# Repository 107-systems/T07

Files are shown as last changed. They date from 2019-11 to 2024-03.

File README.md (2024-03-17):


T07
===

T07 is a wheeled mobile outdoor robotics platform.

### Repositories
* [t07_robot](https://github.com/107-systems/t07_robot): ROS control code for T07 robot.
* [t07_docker](https://github.com/107-systems/t07_docker): Dockerfile and scripts to run T07 control software on [Pika Spark](https://pika-spark.io/).
* [t07_teleop](https://github.com/107-systems/t07_teleop): Keyboard based teleoperation for the T07 mobile outdoor robot.

### 3D-Renderings

<p align="center">
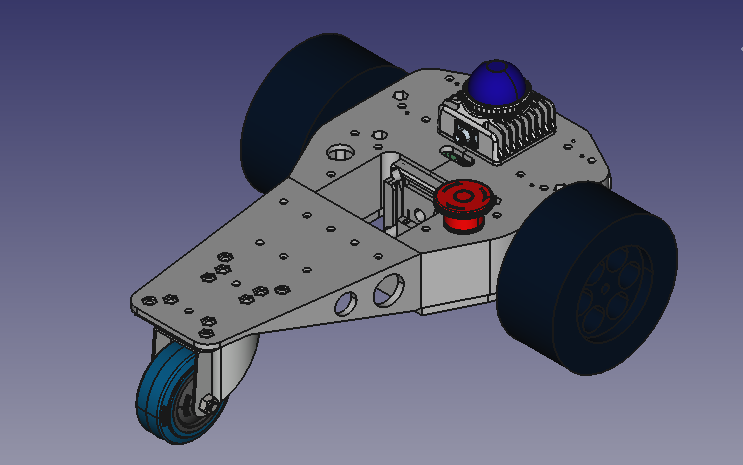
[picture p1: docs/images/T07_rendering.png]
   
</p>

<p align="center">
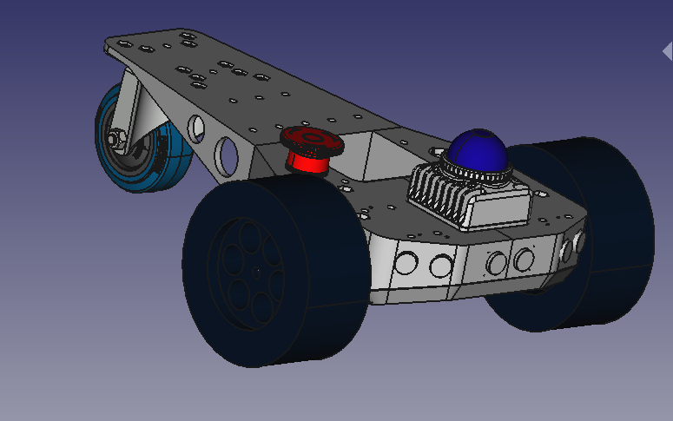
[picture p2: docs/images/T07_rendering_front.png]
   
</p>

<p align="center">
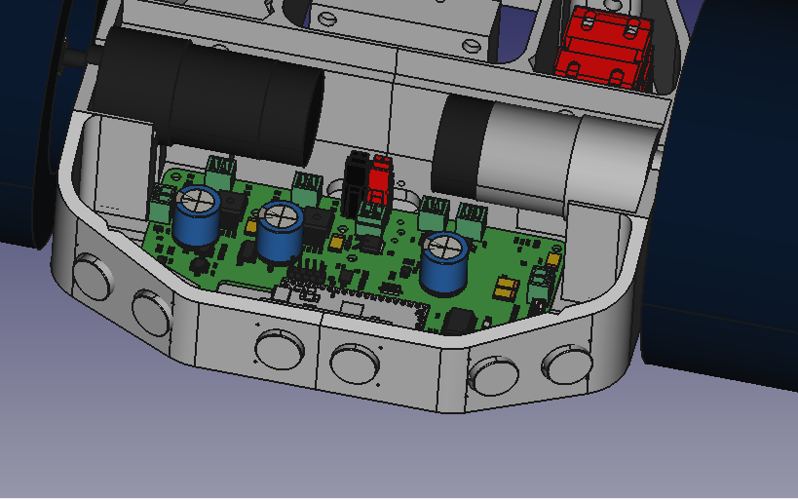
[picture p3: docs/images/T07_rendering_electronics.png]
   
</p>

<p align="center">
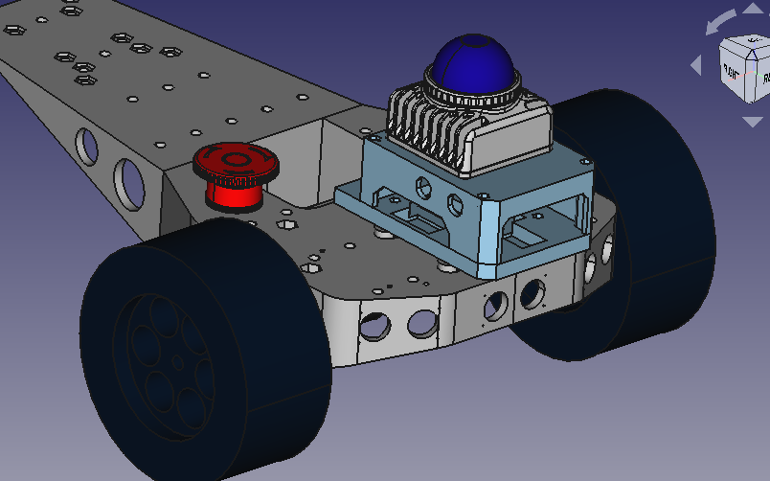
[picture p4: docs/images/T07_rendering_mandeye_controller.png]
   
</p>

## Introduction

The T07 is an outdoor robotics platform intended for participation in contests like Robotem Rovne, Roboorienteering or Robotour but also for general robotic experiments.

There is also a mounting option for the [mandeye-controller](https://github.com/JanuszBedkowski/mandeye_controller).

## Special configurations

### T07 4WD

<p align="center">
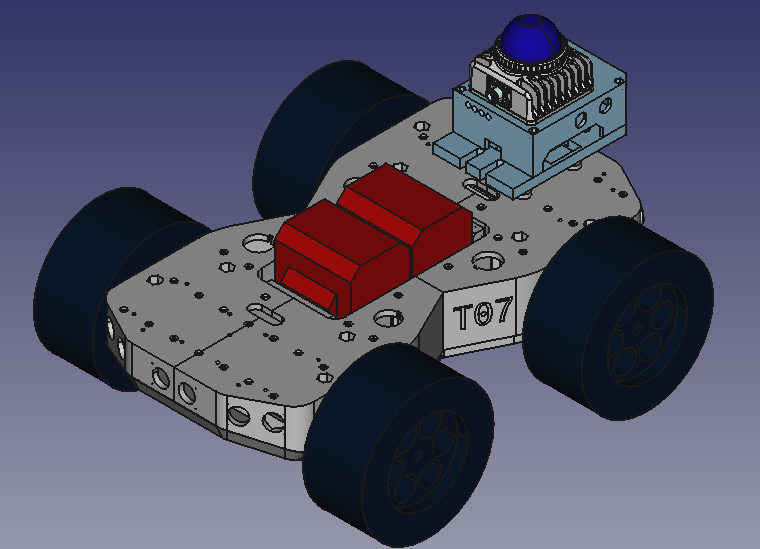
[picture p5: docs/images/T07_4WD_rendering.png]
   
</p>

### T07 low profile

<p align="center">
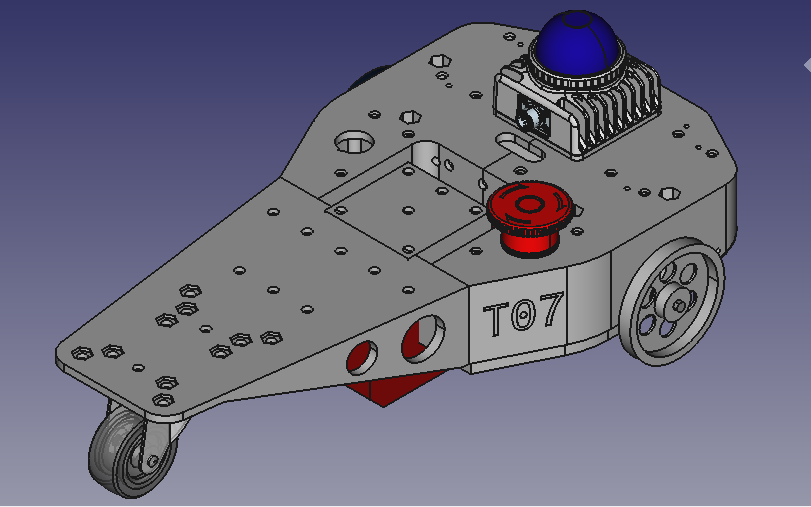
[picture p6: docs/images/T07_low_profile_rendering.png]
   
</p>

<p align="center">
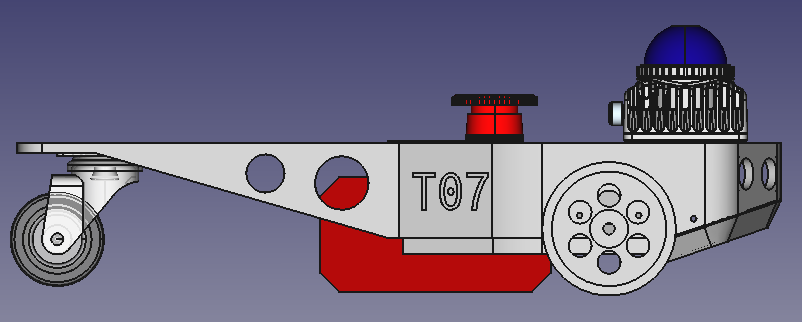
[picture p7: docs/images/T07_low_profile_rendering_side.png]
   
</p>

## Dimensions

The chassis is 40 cm long and 20 cm wide.

The whole robot with ultrasonic sensors is depending on the wheels about 45 cm long and 35 cm wide. The weight is about 1.5 kg.

### Motor shaft and wheel dimension

There are 2 positions to mount the motor shaft.

| Motor shaft | Shaft to roller wheel base | Roller wheel height | Recommended wheel diameter |
|---|---|---|---|
| Upper position | 20 mm | 100 mm (70 mm diameter) | 160 mm |
| Lower position | 34 mm | 100 mm (70 mm diameter) | 132 mm |
| Lower position | 34 mm | 70 mm (50 mm diameter)  | 72 mm |

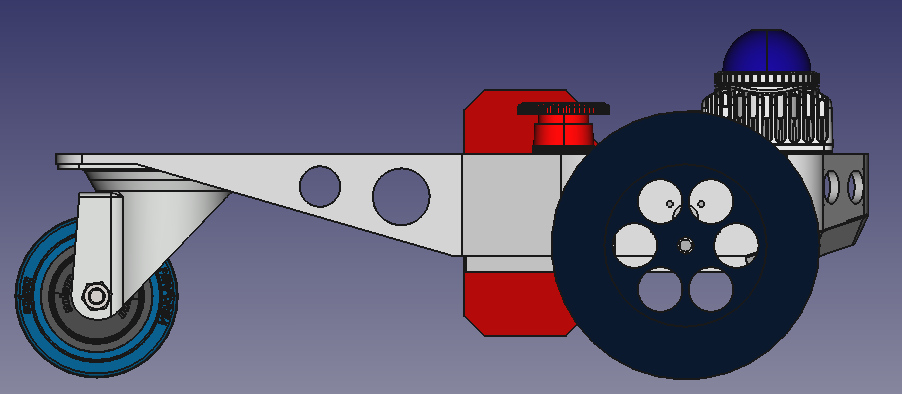
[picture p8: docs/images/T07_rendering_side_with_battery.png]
T07 rendering side view with battery


## Battery

This robot is designed to work with the [Einhell Power X-Change system](https://www.einhell.de/en/battery-system/).

## Assembly

Use flat M6 screw nuts (DIN 439, 3.2 mm high) for the assembly.

## Additional required hardware

### Motors

A motor with a gear ratio of about 1:100 should be ok.

#### Standard

  * https://www.reichelt.de/getriebemotor-39-6-mm-75-1-12-v-dc-gm39-6-75-12v-p159644.html
  * https://www.conrad.de/de/p/getriebemotor-12-v-modelcraft-rb350100-0a101r-1-100-227560.html

#### With encoder

  * https://de.sainsmart.com/products/29-1-metal-gearmotor-365rpm-37dx52l-mm-with-64-cpr-encoder-12v
  * https://eu.robotshop.com/de/products/12v-58rpm-60-1-gear-motor-encoder
  * https://eu.robotshop.com/de/products/12v-26rpm-1201-gear-motor-w-encoder

### Wheels

please pay attention to get the right wheel adapter

#### 132 mm

  * https://www.conrad.de/de/p/reely-1-10-monstertruck-komplettraeder-schwarz-2-st-2249111.html

#### 160 mm

  * https://www.conrad.de/de/p/reely-1-6-buggy-komplettraeder-block-spike-8-speichen-schwarz-glaenzend-2-st-2159621.html

#### 70 mm

  * https://eu.robotshop.com/products/70mm-aluminium-wheel-6mm-bore

### Wheel Adapter

  * https://www.pololu.com/product/2687
  * https://eckstein-shop.de/Pololu-12mm-Hex-Wheel-Adapter-for-6mm-Shaft-Extended-2-Pack

### Roller wheel

#### 100 mm height (70 mm diameter)

  * https://www.pollin.de/p/laufrolle-441614
  * https://radundrolle.de/seiten/Lenkrollen/Vollgummi-Lenkrolle_080.htm

#### 70 mm height (50 mm diameter)

  * https://www.pollin.de/p/masterproof-lenkrolle-kugelgelagert-4054-pvc-oe-50-mm-490596

### On/off Switch

  * https://www.reichelt.de/wippenschalter-rund-ip65-1x-ein-aus-sw-sw-ws-r13-112-a-sw-p105455.html

### Emergency Switch

  * https://www.reichelt.de/not-aus-schalter-yw-40-mm-2-nc-id-yw1bv4e02r-p234555.html
  * https://www.conrad.de/de/p/idec-yw1b-v4e01r-not-aus-schalter-240-v-ac-6-a-1-oeffner-1-st-700792.html
  * https://www.conrad.de/de/p/deca-a20b-v4e11r-not-aus-schalter-mit-kontaktelement-240-v-ac-6-a-1-schliesser-1-oeffner-ip65-1-st-1233793.html

## Electronics and firmware

There are mounting holes for a Raspberry Pi or a [Pika Spark](https://docs.pika-spark.io/) on the controller standoff.

[CyphalRobotController07/CAN](https://github.com/generationmake/CyphalRobotController07-CAN) is the main controller board.

## License

This hardware is licensed under the Creative Commons licence CC-BY-SA 4.0

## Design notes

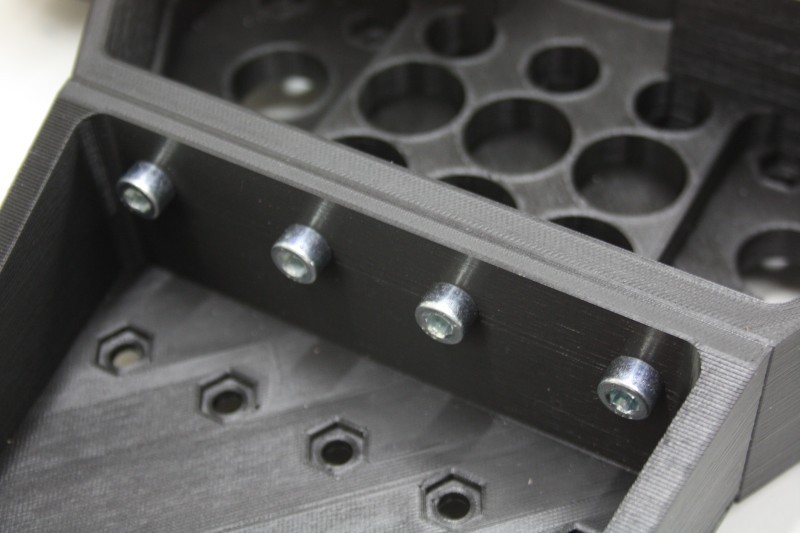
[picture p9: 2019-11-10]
docs/images/chassisconnection_2.jpg

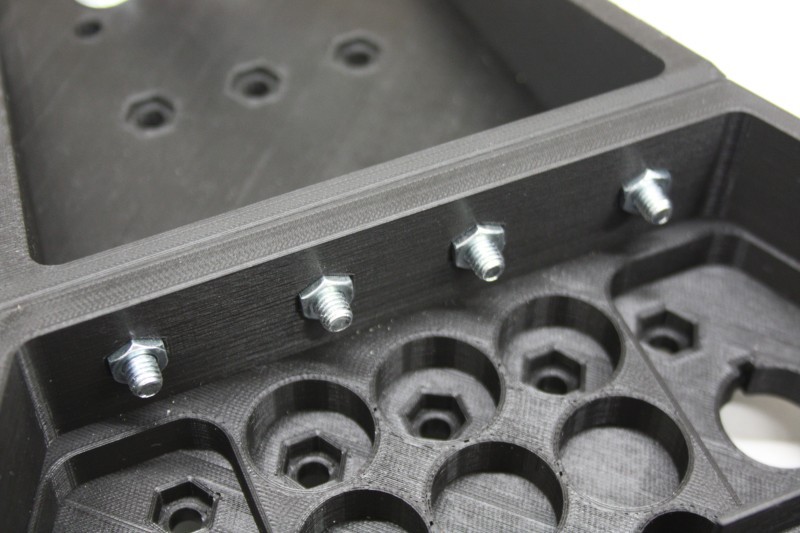
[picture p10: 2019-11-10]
docs/images/chassisconnection_1.jpg

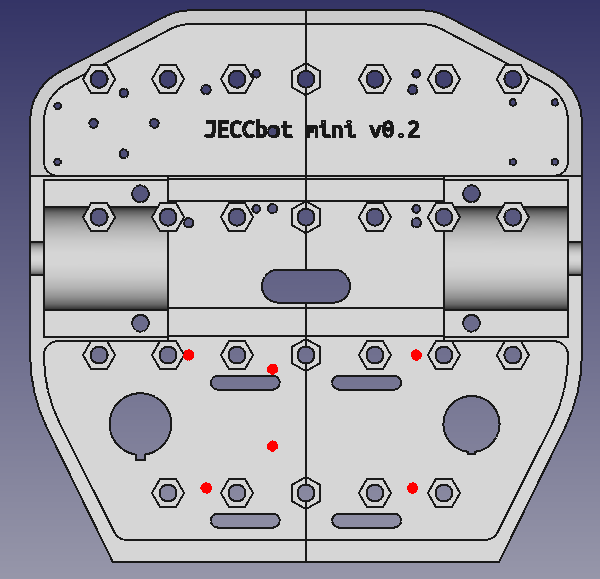
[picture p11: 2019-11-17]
docs/images/mounting/jeccbot_mini_mounting_arduino_bottom.png

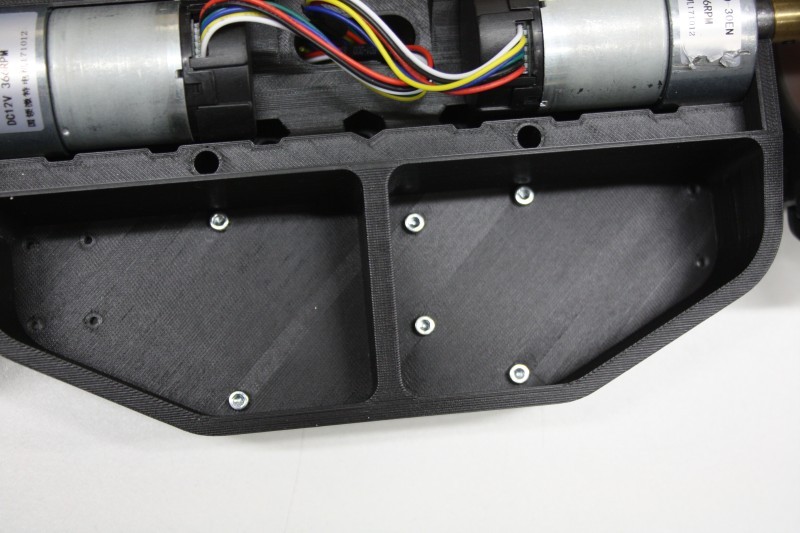
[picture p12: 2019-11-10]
docs/images/arduino_standoff_2.jpg

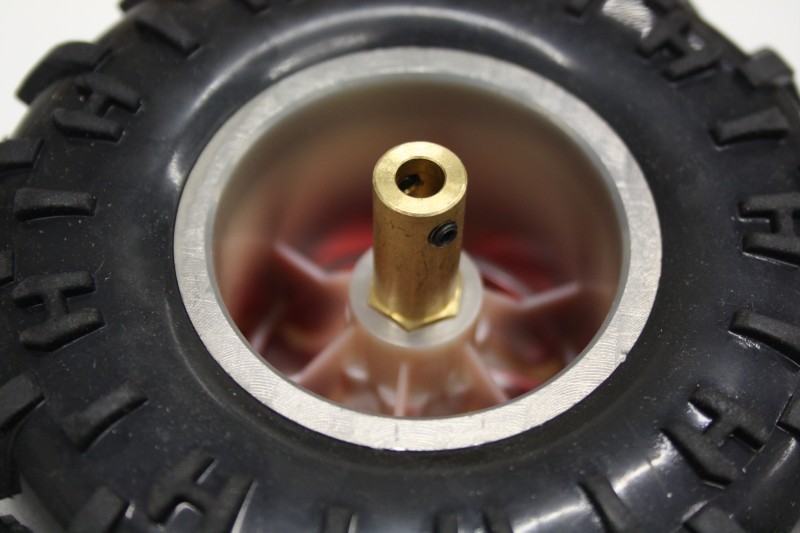
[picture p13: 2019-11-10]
docs/images/wheeladapter.jpg

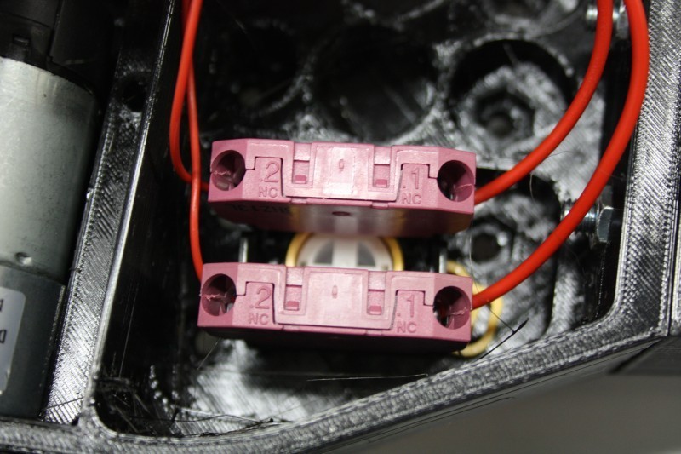
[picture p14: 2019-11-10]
docs/images/emergencybutton_2.jpg

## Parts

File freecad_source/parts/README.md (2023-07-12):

# barrel holder

mount 2 holders 175 mm apart.

use switch
https://www.reichelt.de/schnappschalter-1xum-10a-400vac-flachhebel-mar-1006-1301-p166851.html
https://www.reichelt.de/schnappschalter-1xum-10a-400vac-flachhebel-mar-1006-1401-p166852.html
https://www.reichelt.de/mikroschalter-1x-no-flachhebel-lang-v-163-1c5-p243168.html

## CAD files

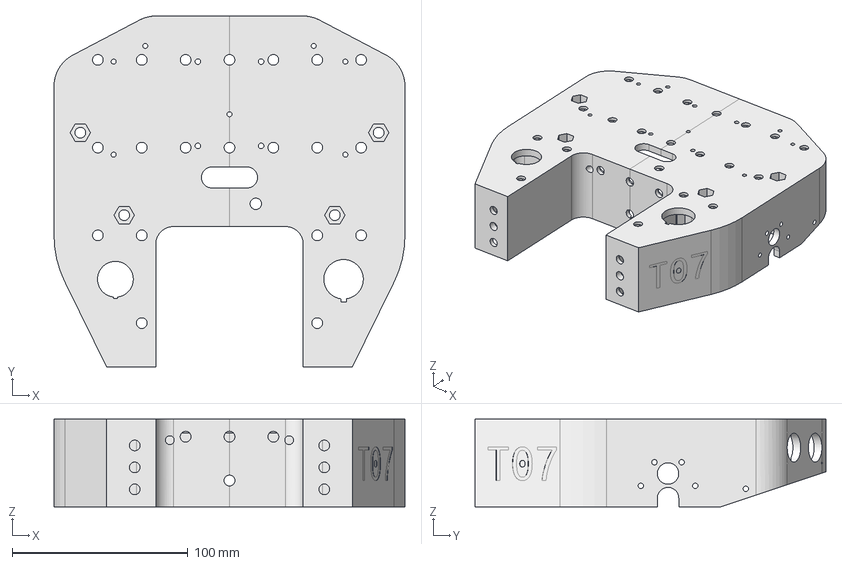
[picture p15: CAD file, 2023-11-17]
productiondata/mainchassis.step
200.0 x 200.0 x 50.0 mm

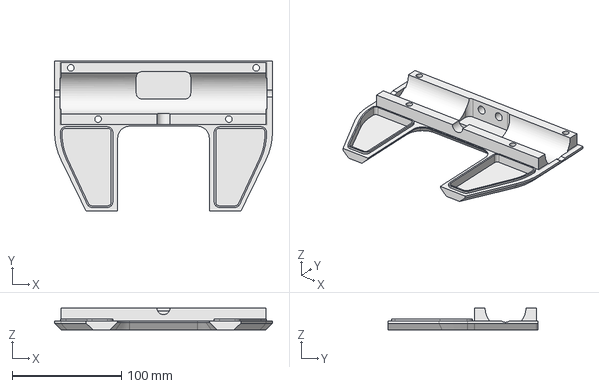
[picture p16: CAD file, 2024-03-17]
freecad_source/parts/T07_motorcover.FCStd
200.0 x 138.0 x 20.0 mm

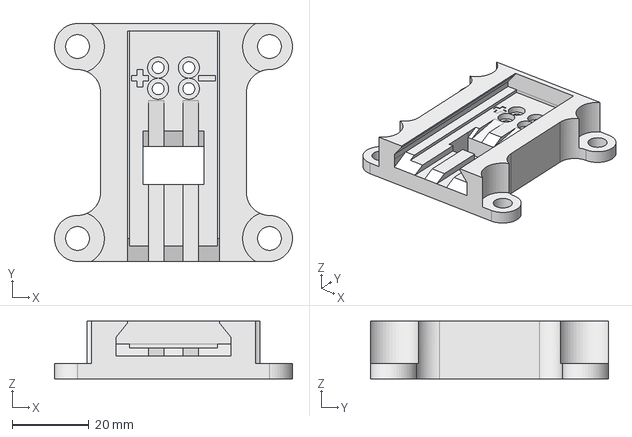
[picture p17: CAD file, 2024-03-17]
freecad_source/parts/mandeye_holder.FCStd
62.0 x 62.0 x 15.0 mm

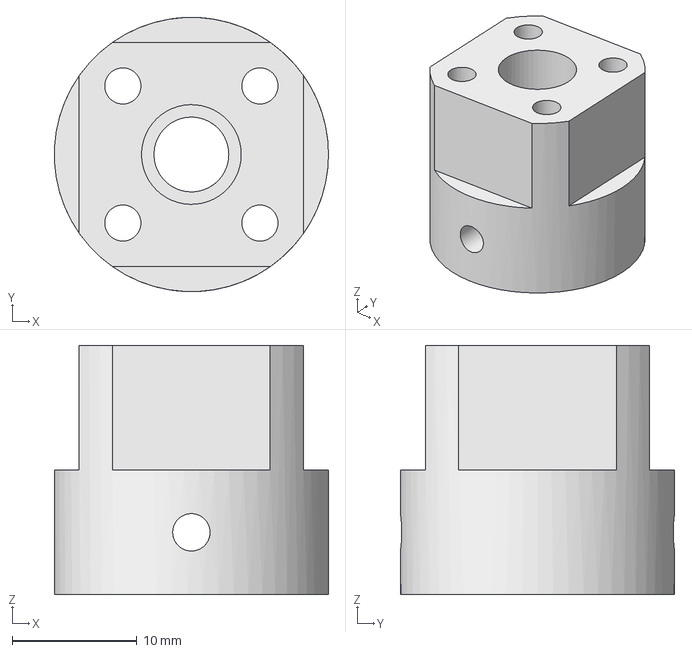
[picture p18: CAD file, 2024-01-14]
freecad_source/parts/T07_wheeladapter_18mm2.FCStd
22.0 x 22.0 x 20.0 mm

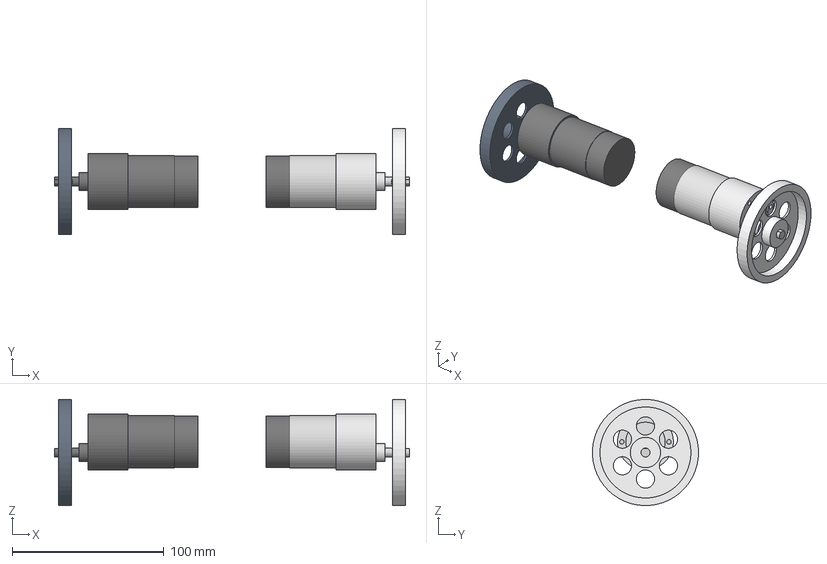
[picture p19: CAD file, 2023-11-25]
freecad_source/parts/motor_wheel_combo_70mm.step
234.0 x 69.9 x 70.0 mm
wheel right (Mirror #2)
Gearmotor_37D_100 v1 (Mirror #3)
wheel right
Gearmotor_37D_100 v1

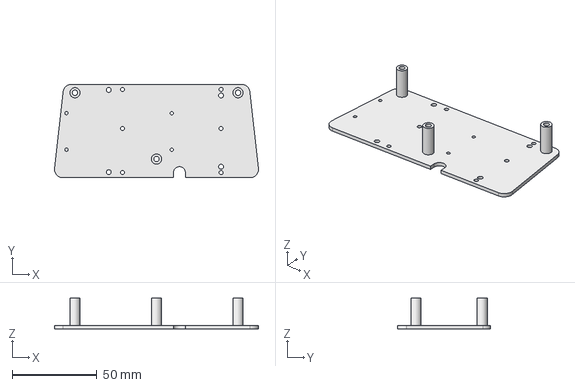
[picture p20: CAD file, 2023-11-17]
productiondata/controller_standoff.step
120.1 x 55.0 x 18.0 mm

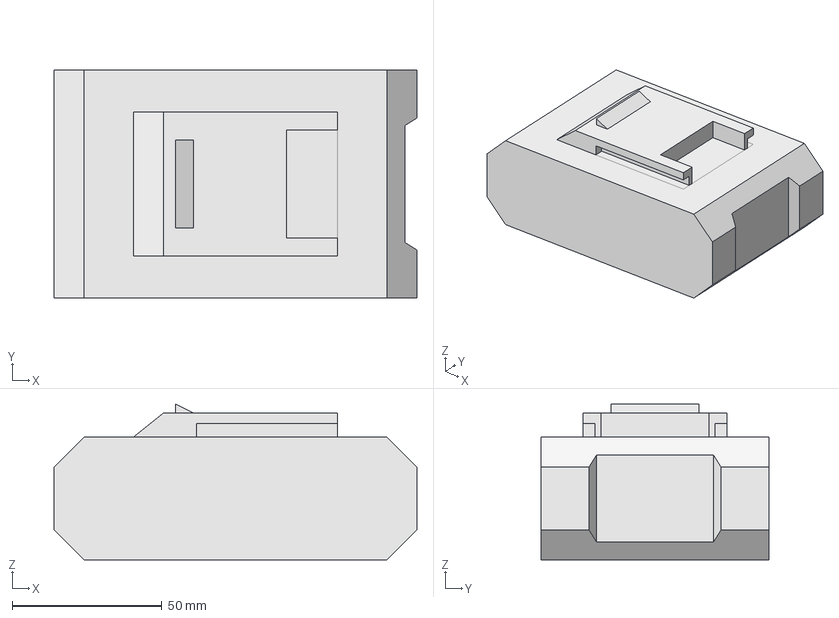
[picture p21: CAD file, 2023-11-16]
productiondata/einhell_power_x-change-2_0ah.step
121.0 x 76.0 x 52.0 mm

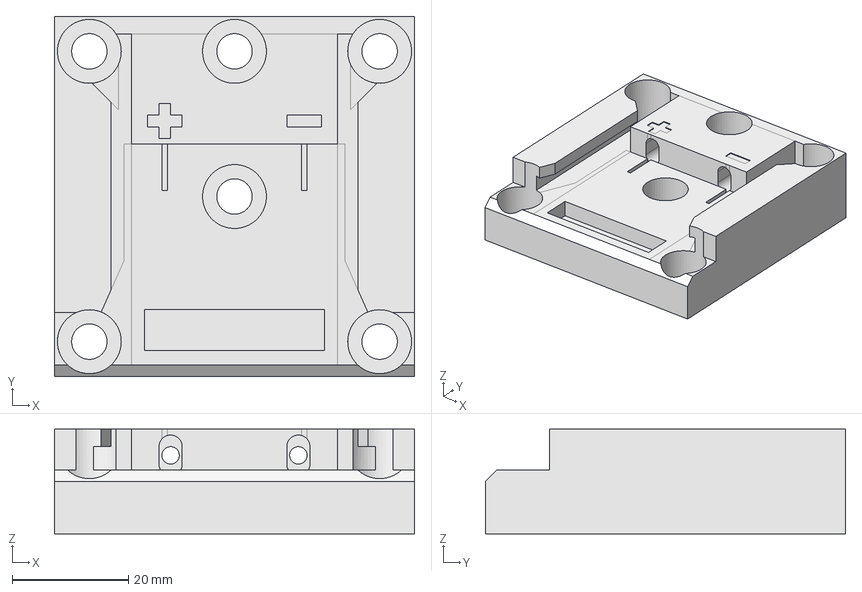
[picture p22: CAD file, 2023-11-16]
productiondata/battery_adapter_einhell_x-change.step
62.0 x 62.0 x 18.0 mm

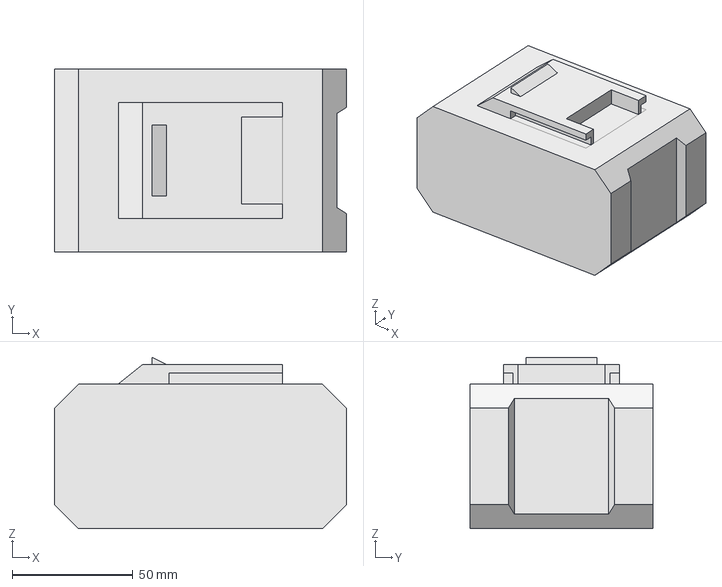
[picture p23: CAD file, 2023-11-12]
productiondata/einhell_power_x-change-4_0ah.step
121.0 x 76.0 x 71.0 mm

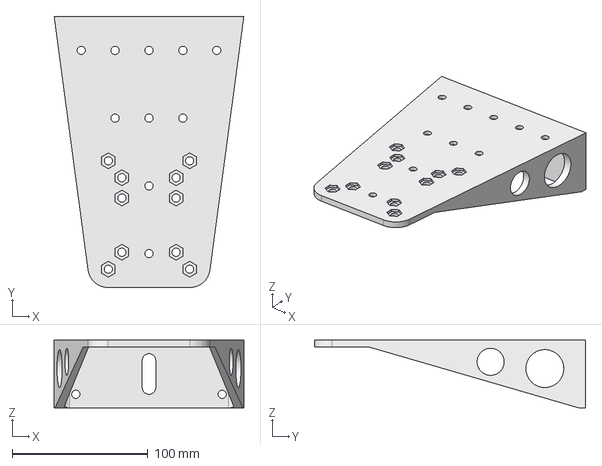
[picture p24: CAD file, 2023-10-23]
freecad_source/parts/T07_rearchassis.FCStd
140.0 x 200.0 x 50.0 mm

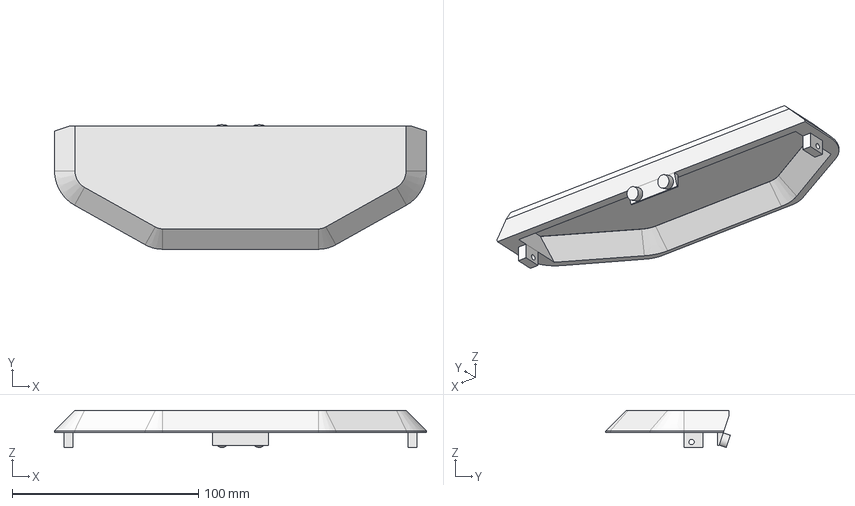
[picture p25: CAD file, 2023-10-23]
productiondata/T07_front_cover.step
200.0 x 67.0 x 20.0 mm

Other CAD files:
freecad_source/parts/T07_mainchassis_assembly.FCStd
productiondata/motorcover.step
productiondata/mandeye_holder.step
productiondata/T07_wheeladapter_18mm2.step
freecad_source/parts/T07_controller_standoff.FCStd
freecad_source/parts/einhell_power_x-change.FCStd
freecad_source/parts/battery_adapter_einhell_x-change.FCStd
freecad_source/parts/T07_front_cover.FCStd
freecad_source/parts/T07_wheeladapter_18mm.FCStd
freecad_source/parts/motor_wheel_combo.FCStd
freecad_source/parts/motor_wheel_combo.step
freecad_source/parts/motor_wheel_combo_70mm.FCStd
productiondata/T07_front_cover.stl
productiondata/T07_wheeladapter_18mm2.stl
productiondata/battery_adapter_einhell_x-change.stl
productiondata/controller_standoff.stl
productiondata/mainchassis.stl
productiondata/mandeye_holder.stl
productiondata/motorcover.stl
productiondata/rearchassis.step
productiondata/rearchassis.stl

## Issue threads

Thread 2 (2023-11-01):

[Bug Report] Links for components are out of date, please update

aentinger, 2023-11-01:
<a href="https://107-systems.org/">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</a>

### :bug: Bug Report

The links to the components required to assemble the platform are partially out-dated, please provide working links.

Closed 2023-11-12.

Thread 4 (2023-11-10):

[Bug Report] Fix the issues of v0.1

generationmake, 2023-11-10:
<a href="https://107-systems.org/">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</a>

### :bug: Bug Report

   - add hole for battery cable
   - add cut out for fuse of CyphalRobotController07/CAN in controller standoff
   - add cut out for power pole connector in motor cover
   - reduce size of motor cover by 0.5 or 1 mm to better slide into mainchassis
   - add cut out for motor shaft into motor cover
   - add cutout for motor connector into mainchassis
   - CyphalRobotController07/CAN collides with screws and nuts for holder for mandeye controller

generationmake, 2023-11-10:
@aentinger
did i miss something?

aentinger, 2023-11-10:
>did i miss something?

No, I believe you did catch everything 😉

generationmake, 2023-11-11:
- slightly increase top opening of mandeye controller holder to let mandeye controller slide in easier

generationmake, 2023-11-11:
- imcrease hole for blade connector in einhell battery holder

generationmake, 2023-11-12:
- add mounting hole for antenna?
  - add mounting holes for beaglebone black?

generationmake, 2023-11-14:
A standard screw nut M6 (DIN 934) is 5 mm heigh. A self securing nut (DIN 985) is 6 mm heigh. A flat nut (DIN 439) is 3.2 mm high.
So I suggest using a flat nut and the right screws and there will be no collision with the controller board.

Closed 2023-11-16.

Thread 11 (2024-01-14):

[Feature Request] Increase width/length of top-plate of motorcover in order to fully cover the main chassis

aentinger, 2024-01-14:
<a href="https://107-systems.org/">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</a>

### ⚡ Feature Request

Increase width/length of top-plate of [motorcover ](https://github.com/107-systems/T07/blob/main/productiondata/motorcover.stl)in order to fully cover the main chassis. No gap should be visible.

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

Closed 2024-03-17.

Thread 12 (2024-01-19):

[Bug Report] Provide bigger cut-outs for motor in bottom plate (collission)

aentinger, 2024-01-19:
<a href="https://107-systems.org/">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</a>

### :bug: Bug Report

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

Closed 2024-03-17.

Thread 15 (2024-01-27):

[Feature Request] Battery mounting option

wuehr1999, 2024-01-27:
<a href="https://107-systems.org/">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</a>

### ⚡ Feature Request

**Please Describe The Problem To Be Solved**

I plan to place a waterproof box on the ```T07``` robot in the following way:

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

**(Optional): Suggest A Solution**

In order to be able to place the box more centered, I would suggest a second mounting position for the battery underneath the robot. The picture shows how the battery could be slided into the mounting position.

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

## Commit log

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2019-10-30 added 3d model of gearmotor, reworked wheel-motor-section
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2019-10-31 reworked rear chassis, added holes, mounting position for battery, position for screw nut
2019-11-01 reworked support structure on main chassis
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2020-01-09 added mounting holes for BNO055 in the center (issue #1)
2020-01-09 corrected mounting holes for ultrasonic sensors
2020-01-10 generated production data for rev 0.3
    [mainchassis.step, mainchassis.stl, motorcover.step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]
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2020-01-18 constructed battery adapter for einhell x-change batteries and added production data
    [battery_adapter_einhell_x-change.step, battery_adapter_einhell_x-change.stl]
2020-01-19 reworked einhell battery adapter to better fit to battery pack
    [battery_adapter_einhell_x-change.step, battery_adapter_einhell_x-change.stl]
2020-01-23 updated battery adapter, made holes slightly bigger, improved electrical contacts, moved arretation holes
    [battery_adapter_einhell_x-change.step, battery_adapter_einhell_x-change.stl]
2020-02-09 made production data for chassis with NEMA17 stepper motor
    [mainchassis_NEMA17.step, mainchassis_NEMA17.stl]
2020-05-10 added test files with Assembly4 of FreeCAD 0.19
    [JECCbot_complete.FCStd, JECCbot_mini_mainchassis_assembly.FCStd, testbot.FCStd]
2020-05-10 added JECCbot ECU case for test
    [JECCbot_complete.FCStd, case.FCStd]
2020-05-10 updated moutning of ultra sonic sensors
    [JECCbot_mini_mainchassis_assembly.FCStd]
2020-05-10 added NEMA17 chassis stl
    [JECCbot_complete.FCStd, mainchassis_NEMA17.stl]
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2020-07-21 generated stl for barrelholder
    [barrelholder.stl]
2020-07-21 updated barrel holder to better fit to barrel and added mounting holes for switch
    [barrel_holder.FCStd]
2020-07-21 moved switch to the side
    [barrel_holder.FCStd]
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2023-07-09 removed testbot because this one seems not to be necessary
    [testbot.FCStd]
2023-07-09 removed JECCbot_complete because this one also seems not to be necessary
    [JECCbot_complete.FCStd]
2023-07-09 renamed Assembly4 to parts because this folder will hold all single parts of the robot
    [JECCbot_mini_mainchassis_assembly.FCStd, barrel_holder.FCStd, case.FCStd]
2023-07-09 moved parts into single Freecad files
    [JECCbot_mini_motorcover.FCStd, JECCbot_mini_rearchassis.FCStd, JECCbot_mini_wheeladapter_18mm.FCStd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]
2023-07-09 removed case.FCStd because this is already in https://github.com/wuehr1999/JECCbotECU
    [case.FCStd]
2023-07-09 rebuilt the JECCbot_mini with single step files
    [motor_wheel_combo.step]
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2023-07-09 redraw of main chassis
    [JECCbot_mini_mainchassis_assembly.FCStd, mainchassis.step, mainchassis.stl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]
2023-07-15 reworked main chassis
    [JECCbot_mini_mainchassis_assembly.FCStd, mainchassis.step, mainchassis.stl]
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2023-10-03 adjusted cut out and mounting options for CyphalRobotController07/CAN
    [T07_mainchassis_assembly.FCStd, T07_motorcover.FCStd, mainchassis.step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]
2023-10-03 reworked connection between mainchassis and rearchassis
    [T07_mainchassis_assembly.FCStd, T07_rearchassis.FCStd, mainchassis.step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]
2023-10-03 reworked connection for battery holder
    [T07_mainchassis_assembly.FCStd, battery_adapter_einhell_x-change.FCStd, battery_adapter_einhell_x-change.step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]
2023-10-03 added PikaSpark and mounting support
    [T07_controller_standoff.FCStd, controller_standoff.step]
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2023-10-10 reworked controller standoff
    [T07_controller_standoff.FCStd, controller_standoff.step]
2023-10-11 reworked mounting holes
    [T07_mainchassis_assembly.FCStd, mainchassis.step, mainchassis.stl]
2023-10-15 updated the mandeye holder and added the mandeye controller to the complete setup
    [mandeye_holder.FCStd, mandeye_holder.step, mandeye_holder.stl]
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2023-10-18 removed barrel holder, not necessary for this project
    [barrel_holder.FCStd]
2023-10-18 updated some stl files
    [battery_adapter_einhell_x-change.stl, rearchassis.stl]
2023-10-18 reworked motorcover
    [T07_motorcover.FCStd, motorcover.step, motorcover.stl]
2023-10-19 first draft of a front cover
    [T07_front_cover.FCStd, T07_front_cover.step, T07_front_cover.stl]
2023-10-19 reworked mounting options for the front cover
    [T07_front_cover.FCStd, T07_front_cover.step, T07_front_cover.stl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]
2023-10-19 updated controller standoff, added mounting holes for PikaSpark and Raspberry Pi
    [T07_controller_standoff.FCStd, controller_standoff.step, controller_standoff.stl]
2023-10-19 added hole for cables from mainchassis to rearchassis
    [T07_mainchassis_assembly.FCStd, mainchassis.step, mainchassis.stl]
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2023-11-12 added 3d model of einhell battery
    [einhell_power_x-change_4_0ah.FCStd, einhell_power_x-change_4_0ah.step]
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2023-11-12 added 3d model of einhell 2 ah battery
    [einhell_power_x-change-2_0ah.step, einhell_power_x-change-4_0ah.step, einhell_power_x-change.FCStd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]
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2023-11-12 updated battery holder, made hole for blade connector longer, additional mounting hole
    [battery_adapter_einhell_x-change.FCStd, battery_adapter_einhell_x-change.step, battery_adapter_einhell_x-change.stl]
2023-11-13 updated mainchassis, added coutout for motor connector and hole for battery cable
    [T07_mainchassis_assembly.FCStd, mainchassis.step, mainchassis.stl]
2023-11-13 updated motorcover, added cutout for motor shaft, reduced size to better slide in
    [T07_motorcover.FCStd]
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2023-11-15 made mandeye holder 2mm higher to simplify mounting of cables
    [mandeye_holder.FCStd, mandeye_holder.step, mandeye_holder.stl]
2023-11-16 updated controller standoff, added cut out for fuse
    [T07_controller_standoff.FCStd, controller_standoff.step, controller_standoff.stl]
2023-11-16 updated main chassis, increased pocket for grid screw nuts from 2 mm to 3 mm so that flat nuts completely sink in
    [T07_mainchassis_assembly.FCStd, mainchassis.step, mainchassis.stl]
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2023-11-16 updated controller standoff, added mounting options for Raspberry Pi Zero and Beaglebone Black
    [T07_controller_standoff.FCStd, controller_standoff.step, controller_standoff.stl]
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2023-11-25 added motor wheel combo with 70 mm wheels
    [motor_wheel_combo_70mm.FCStd, motor_wheel_combo_70mm.step]
2024-01-14 added 3d printable design or 18 mm wheeladapter (#9)
    [T07_wheeladapter_18mm2.FCStd, T07_wheeladapter_18mm2.step, T07_wheeladapter_18mm2.stl]
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
